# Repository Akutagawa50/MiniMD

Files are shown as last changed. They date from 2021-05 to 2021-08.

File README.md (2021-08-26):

# MiniMD
低電流用モータドライバ回路のKicadデータ

# 仕様
* 最大電流 5.3[A]
* 最大電圧 25[V]
* 2ピンで制御可能
* フォトカプラでマイコンとモータドライバを絶縁

<!--
# 変更メモ
- [x] RESET は電源からプルアップ
- [x] VDSTHを5V->1K->VDSTH->10k->GND
- [x] VREGの静電容量を1uFに変更
- [x] 5Vにコンデンサ1uFを入れる
- [x] リセットボタンのフットプリント変更
-->
# 信号線メモ
PHASE, PWMHはプルアップ
| | SR  | PWML |
| ---- | --- | ---- |
| 停止 | 0 | 0 |
| 停止 | 1 | 0 |
| 正転 | 0 | 1 |
| 逆転 | 1 | 1 |

# 回路図

https://github.com/Akutagawa50/MiniMD/blob/0ade2ae8e789b871e048b73d981d6f0f50aa8e78/circuit.pdf

# 使用部品
## 半導体素子
### ゲートドライバ
フルブリッジMOSFETドライバ　A3921KLPTR－T

https://akizukidenshi.com/catalog/g/gI-12293/

[](https://akizukidenshi.com/catalog/g/gI-12293/)

### MOSFET
Nch MOSFET 60V 5.3A SI4900DY

https://akizukidenshi.com/catalog/g/gI-09931/

[](https://akizukidenshi.com/catalog/g/gI-09931/)

### フォトカプラ
フォトカプラ　赤外LED＋フォトトランジスタ　TLP291（GB）

https://akizukidenshi.com/catalog/g/gI-07189/

[](https://akizukidenshi.com/catalog/g/gI-07189/)

### ショットキーバリアダイオード
表面実装用ショットキーダイオード　80V1A　MS18F　（20個入）

https://akizukidenshi.com/catalog/g/gI-06190/

[](https://akizukidenshi.com/catalog/g/gI-06190/)

### LED
青色チップLED［1608］ OSBL1608　（20個入）

https://akizukidenshi.com/catalog/g/gI-03982/

[](https://akizukidenshi.com/catalog/g/gI-03982/)

## 抵抗
超精密級　金属皮膜チップ抵抗器　1608　1/10W1kΩ±0.1%　（5個入）

https://akizukidenshi.com/catalog/g/gR-11790/ (5個)

https://akizukidenshi.com/catalog/g/gR-14122/ (5000個)
<!--
[<img src="https://akizukidenshi.com/img/goods/C/R-11790.jpg" width=200>](https://akizukidenshi.com/catalog/g/gR-11790/)
-->
[](https://akizukidenshi.com/catalog/g/gR-14122/)

<br>

チップ抵抗　1/10W100kΩ　（5000個入）

https://akizukidenshi.com/catalog/g/gR-15321/

[](https://akizukidenshi.com/catalog/g/gR-15321/)
<br>

チップ抵抗　1/10W10kΩ　（2500個入）

https://akizukidenshi.com/catalog/g/gR-06103/

[](https://akizukidenshi.com/catalog/g/gR-06103/)
<br>
チップ抵抗　1/10W47Ω　（2500個入）

https://akizukidenshi.com/catalog/g/gR-06470/

[](https://akizukidenshi.com/catalog/g/gR-06470/)

## コンデンサ
### 電解コンデンサ
チップ電解コンデンサー　220μF50V　（ニチコン・URシリーズ）（５個入）

https://akizukidenshi.com/catalog/g/gP-04577/

[](https://akizukidenshi.com/catalog/g/gP-04577/)

### チップコンデンサ
<br>
チップ積層セラミックコンデンサー　0.47μF50V　X7R　3216　（10個入）

https://akizukidenshi.com/catalog/g/gP-14576/

[](https://akizukidenshi.com/catalog/g/gP-14576/)

チップ積層セラミックコンデンサー　1μF16V F 1608　（100個入）

https://akizukidenshi.com/catalog/g/gP-13373/ (100個)

https://akizukidenshi.com/catalog/g/gP-00492/ (4000個)

[](https://akizukidenshi.com/catalog/g/gP-13373/)

[](https://akizukidenshi.com/catalog/g/gP-00492/)

## コネクタ
XHコネクタ　ハウジング　2P　XHP-2

https://akizukidenshi.com/catalog/g/gC-12255/

[](https://akizukidenshi.com/catalog/g/gC-12255/)
<br>

XHコネクタ　ハウジング　5P　XHP-5

https://akizukidenshi.com/catalog/g/gC-12258/

[](https://akizukidenshi.com/catalog/g/gC-12258/)
<br>

XHコネクタ　ベース付ポスト　サイド型　2P　S2B－XH－A（LF）（SN）

https://akizukidenshi.com/catalog/g/gC-12262/

[](https://akizukidenshi.com/catalog/g/gC-12262/)
<br>

XHコネクタ　ベース付ポスト　サイド型　3P　S3B-XH-A（LF）（SN）

https://akizukidenshi.com/catalog/g/gC-12263/

[](https://akizukidenshi.com/catalog/g/gC-12263/)
<br>

XHコネクタ　ハウジング用コンタクト　SXH－001T－P0.6　（100個入）

https://akizukidenshi.com/catalog/g/gC-12265/

[](https://akizukidenshi.com/catalog/g/gC-12265/)

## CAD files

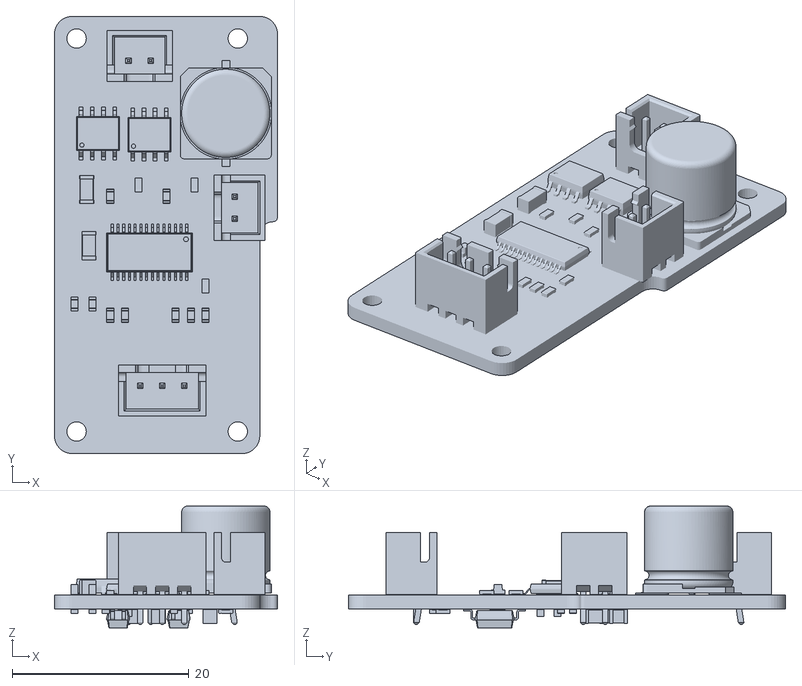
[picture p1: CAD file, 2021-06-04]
MiniMD_1bord.stl
25.2 x 49.5 x 13.8

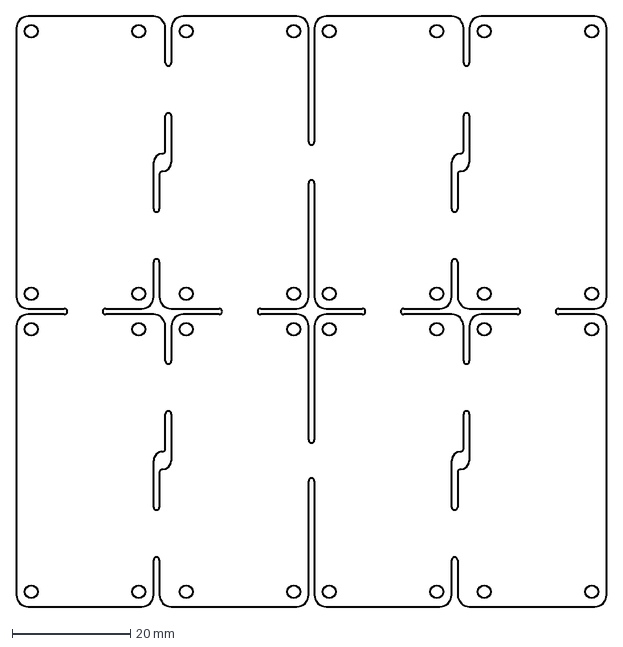
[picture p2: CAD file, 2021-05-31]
Part1.dxf
100.0 x 100.0 mm

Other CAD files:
OldVersions/Part1.0004.dwg
MiniMD_1bord.ipt
OldVersions/Part1.0007.ipt
Part1.dwg
Part1.ipt

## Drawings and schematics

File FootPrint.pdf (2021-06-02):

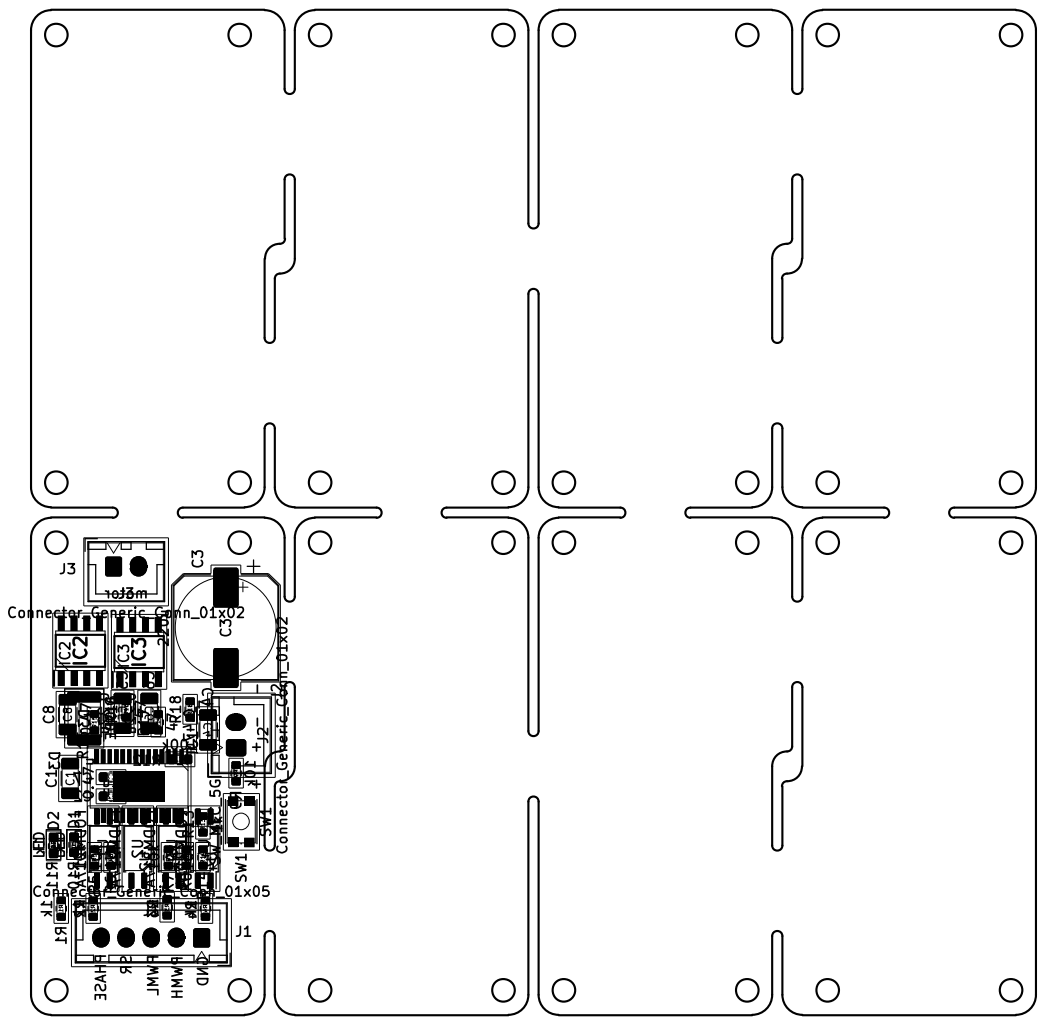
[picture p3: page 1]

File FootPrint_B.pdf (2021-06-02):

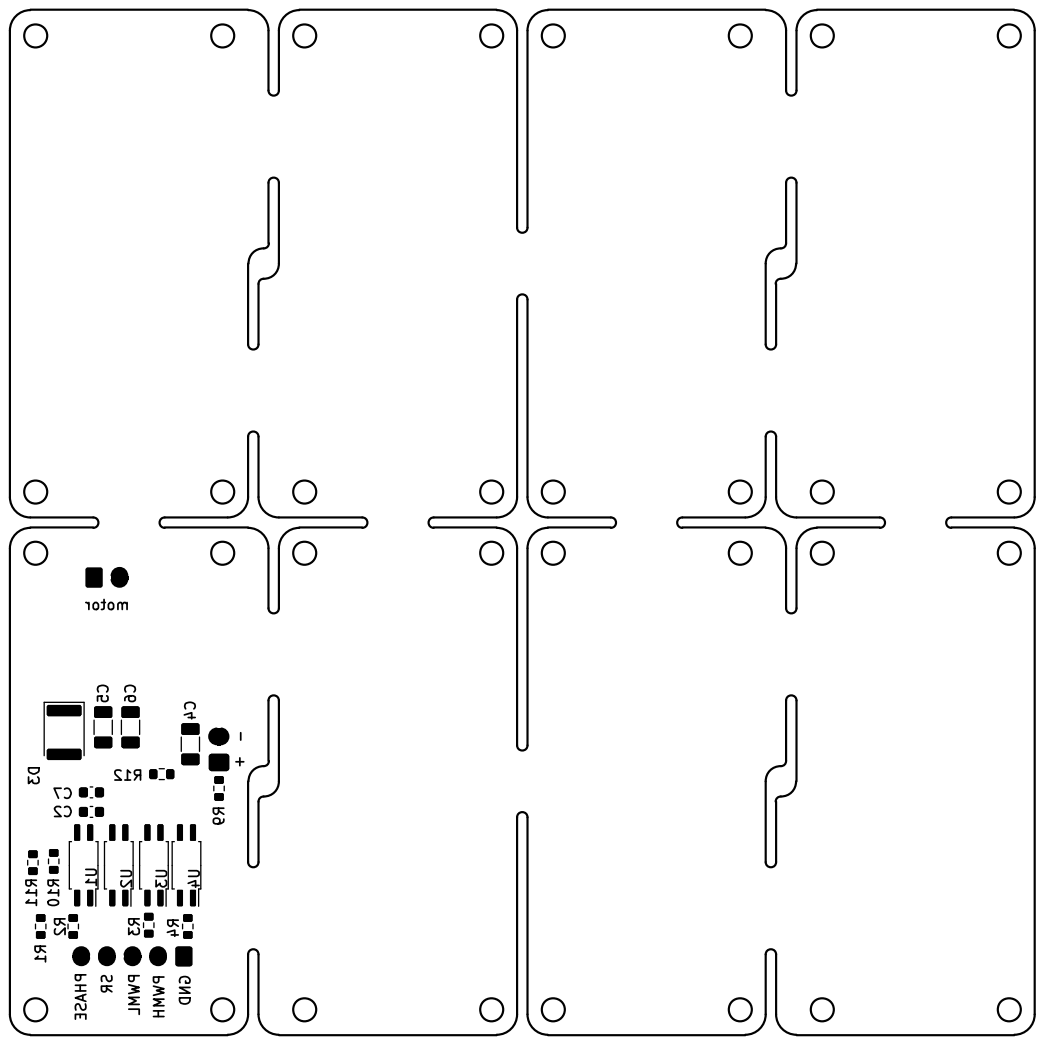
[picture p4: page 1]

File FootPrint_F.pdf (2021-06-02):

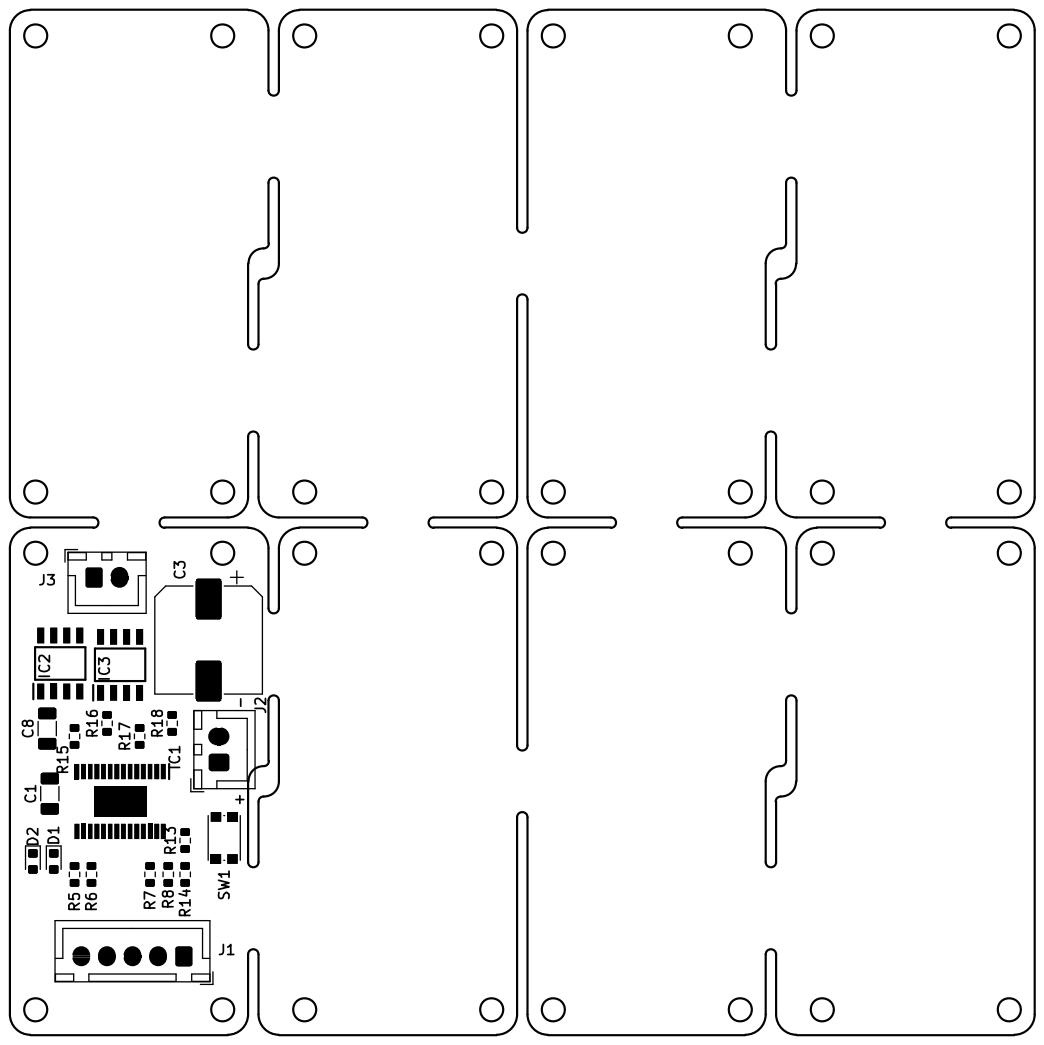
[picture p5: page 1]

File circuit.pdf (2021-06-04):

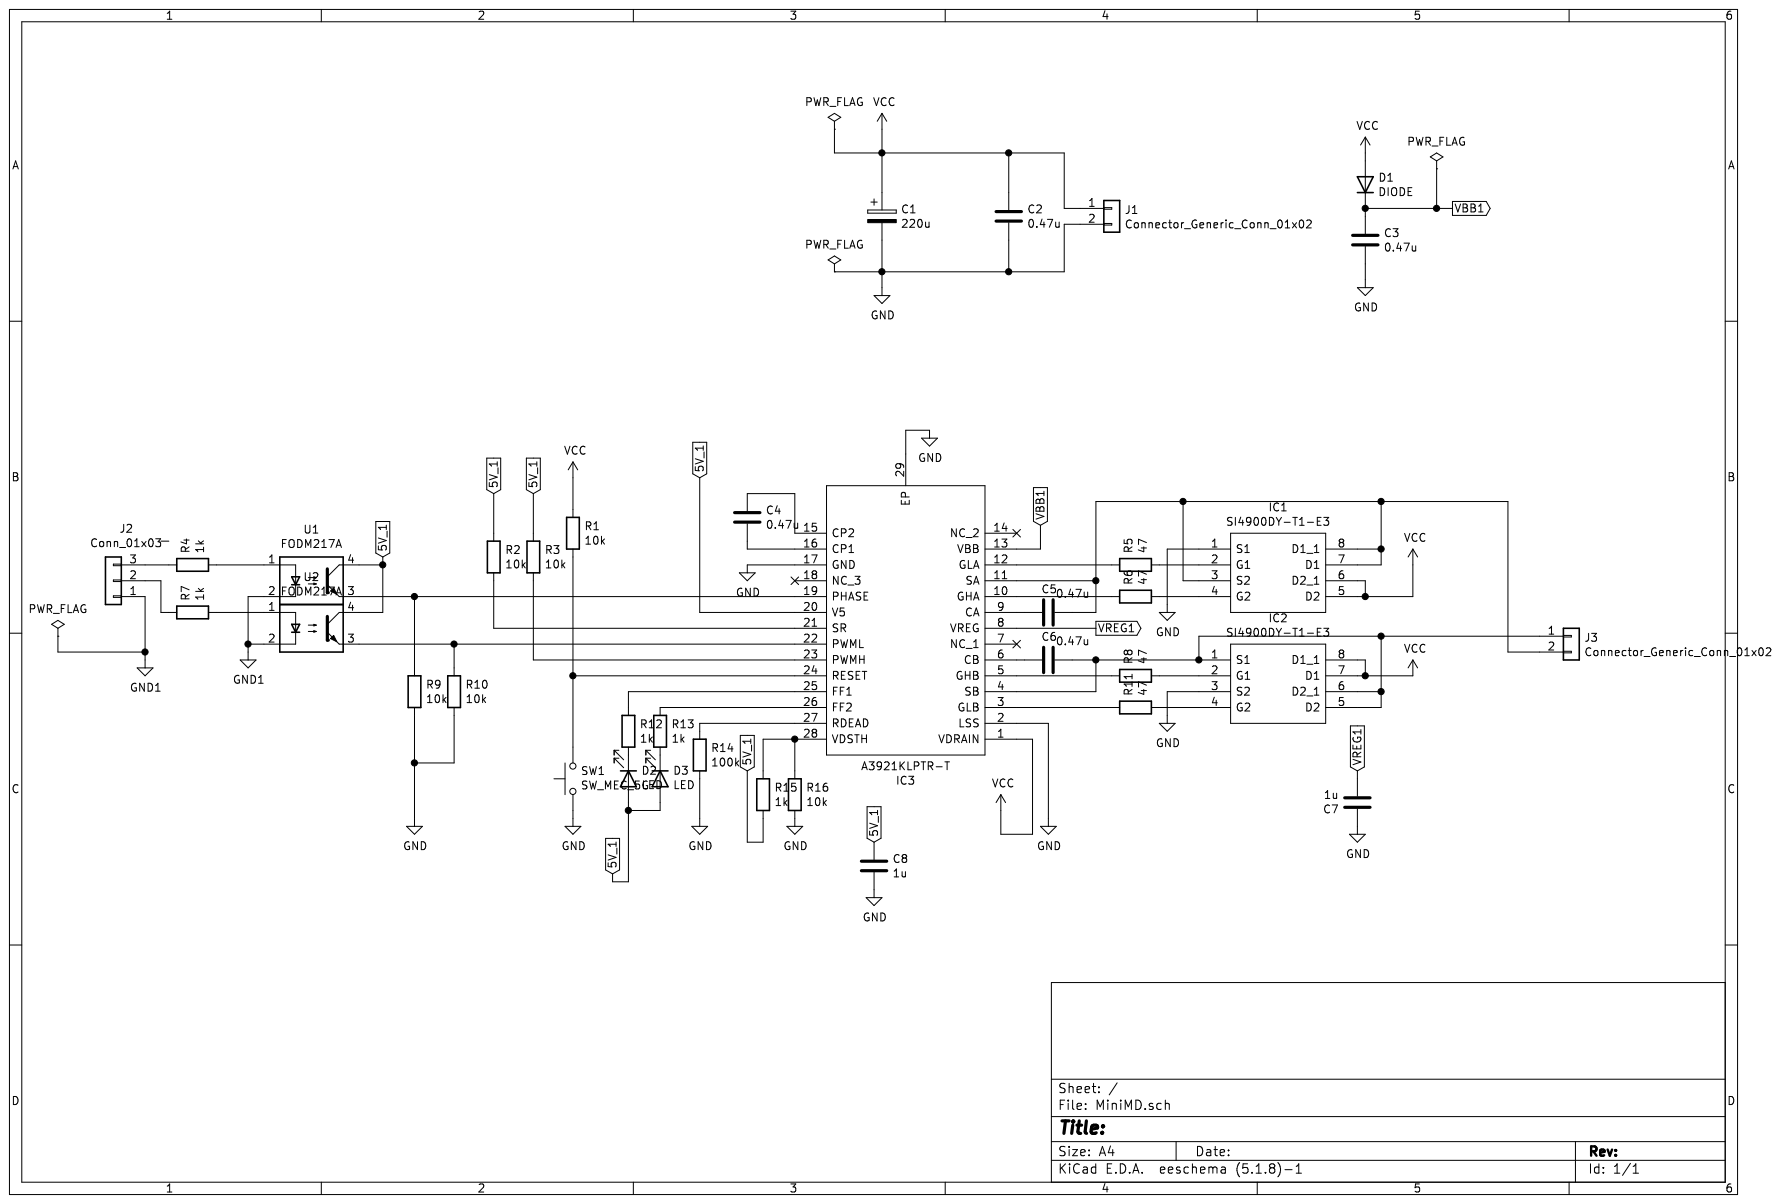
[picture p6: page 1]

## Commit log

2021-05-31 upload new file
    [MD2.sch, MiniMD.kicad_pcb, MiniMD.sch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]
2021-06-02 シンボルの挿入まで完成
    [MD2.sch, MiniMD.kicad_pcb, MiniMD.sch]
2021-06-04 3Dモデルをアップ
    [MiniMD_1bord.stl]
2021-06-04 回路図を追加
2021-06-04 基板を調整
    [MiniMD.sch, MiniMD_1bord.ipt, MiniMD_1bord.stl]
